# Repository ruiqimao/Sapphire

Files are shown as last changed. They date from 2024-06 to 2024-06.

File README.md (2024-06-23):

# Sapphire

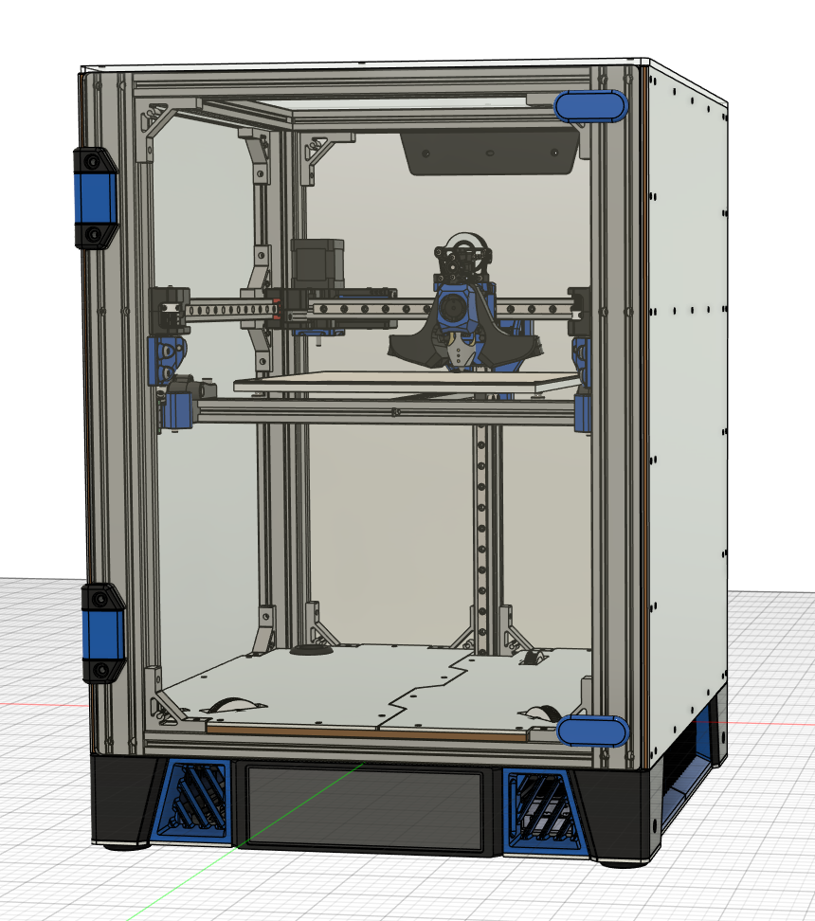
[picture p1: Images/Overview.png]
Overview


Sapphire is a 250x250x230 CoreXY printer primarily featuring components from other projects:

* [Monolith gantry](https://github.com/CloakedWayne/Monolith_Gantry_V2-VT)
* [Archetype toolhead](https://github.com/Armchair-Heavy-Industries/Archetype)
* [Annex Engineering K3 Z system](https://github.com/Annex-Engineering/Gasherbrum-K3)
* [Voron Trident bed](https://github.com/VoronDesign/Voron-Trident)
* 4040/2020 frame members
* Aluminum structural panels
* Slide out electronics bay
* Dual PSUs for mixed 24V and 48V components
* Dual SSRs for optional chamber heating
* [7.9" Waveshare DSI display](https://www.waveshare.com/7.9inch-dsi-lcd.htm)

## CAD

* CAD drawings for original design elements are included in [CAD/Base/Sapphire.zip](CAD/Base/Sapphire.zip).
* Monolith and Archetype components can be found in their respective repositories.
* Modified version of K3Z can be found in [CAD/Z Components/Z Components.zip](<CAD/Z Components/Z Components.zip>), along with a copy of the Annex Engineering license agreement.

## STLs

No STLs are provided. Everything is available from CAD or external repositories.

## Misumi codes

The extrusions and brackets used for the frame, bed, and electronics are:

### Frame
```
4x HFS5-4040-550-SC-LCP-RCP-AV360
9x HFS5-2040-370-TPW-SC
1x HFS5-2040-370-TPW-SC-AH185
1x HFS5-2040-330-TPW-SC
1x HFS5-2020-240-SC
1x HFS5-2020-370-SC
```

### Bed
```
1x HFS5-2020-340-TPW-SC-AH170
1x HFS5-2020-255-TPW-SC
```

### Electronics
```
2x HFS5-2020-300
```

### Corner brackets
```
31x HBKUS5
```

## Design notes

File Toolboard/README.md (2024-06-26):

# Sapphire Toolboard

> [!WARNING]
> Archetype is in beta and is subject to change. Use this toolboard knowing that compatibility may break in the future.

<p float="left">
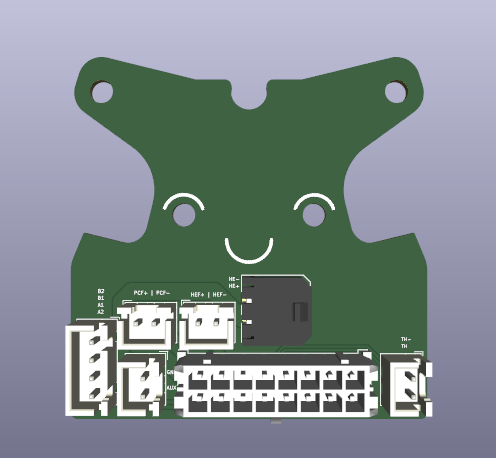
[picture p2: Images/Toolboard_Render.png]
  
  
</p>

These are the files used to produce and mount the toolhead PCB used in Sapphire.

## Production requirements

* 1.6mm thick
* 2 layers
* 1oz minimum (2oz preferred)

## Mounting

The toolboard is clamped between the Sherpa Mini and extruder block, as shown here:

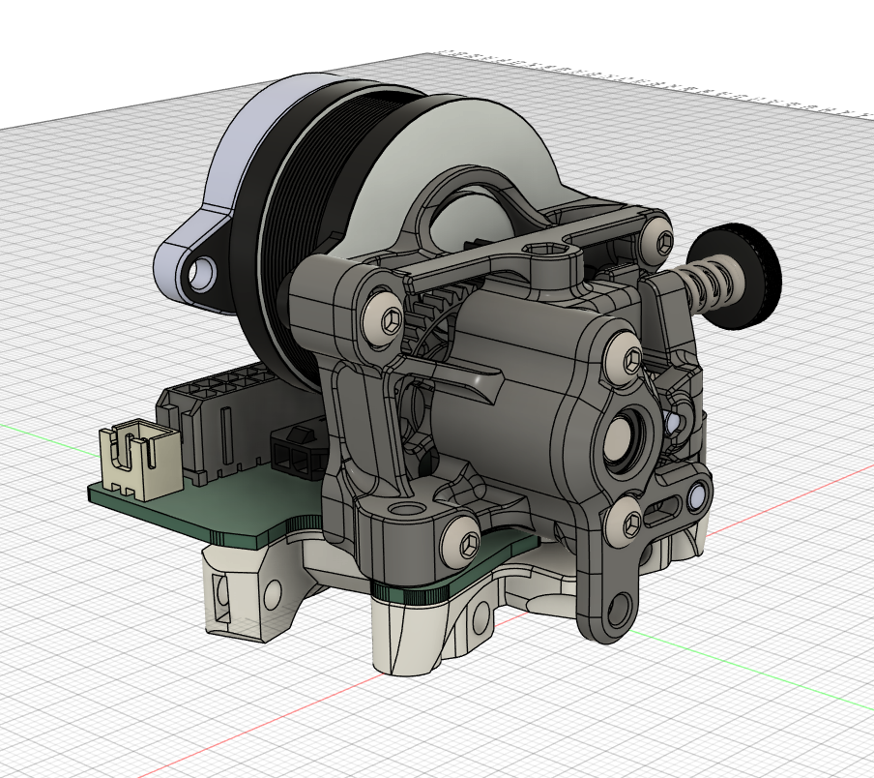
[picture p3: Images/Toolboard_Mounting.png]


## STLs

* K_Face.stl: An altered K-Face for the Sherpa Mini is necessary due to the thickness of the PCB.
* Strain_Relief.stl: Mounted to the back of the stepper motor to provide strain relief.

## Harness and distribution board

Pinout and harness compatible with [Xol PCB](https://github.com/ruiqimao/VoronStuff/tree/main/Xol_PCB).

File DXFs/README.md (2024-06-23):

# DXFs

## Materials

### 3.2mm Aluminum
* Back
* Deck_Left
* Deck_Right
* Electronics
* Side
* Skirt

### 5.6mm Polycarbonate
* Front Door
* Top

## Notes

* Two copies of Side_x2.dxf and Skirt_x2.dxf are needed.
* Electronics.dxf contains holes meant to be tapped for PSU and SSR mounting:
  * M3: 2.6mm holes
  * M4: 3.41mm holes
* Front_Door.dxf requires the holes mounted to the hinges to be countersunk.

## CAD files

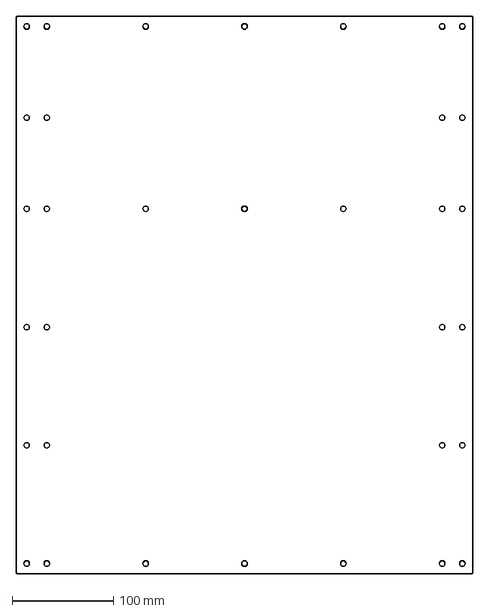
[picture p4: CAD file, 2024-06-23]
DXFs/Side_x2.dxf
450.0 x 550.0 mm

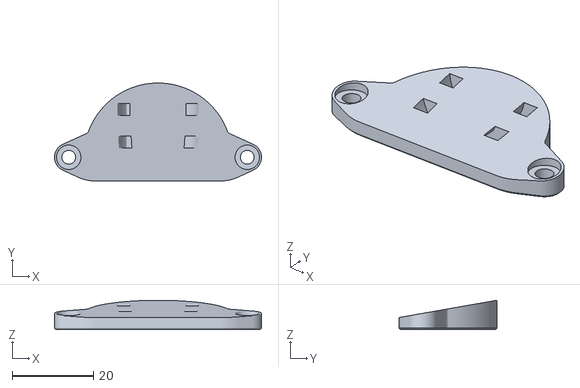
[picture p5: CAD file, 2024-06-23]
Toolboard/STLs/Strain_Relief.stl
50.9 x 24.1 x 7.25

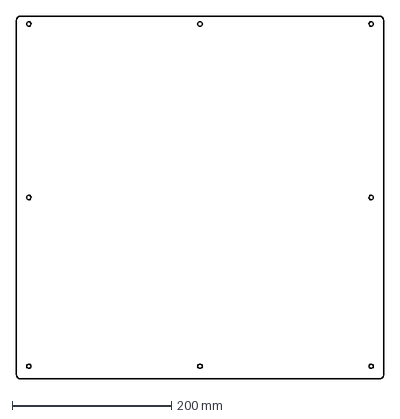
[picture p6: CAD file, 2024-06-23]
DXFs/Top.dxf
462.0 x 456.0 mm

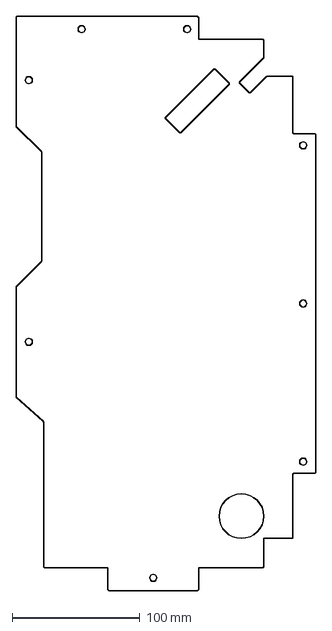
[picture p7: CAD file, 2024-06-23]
DXFs/Deck_Left.dxf
235.0 x 450.0 mm

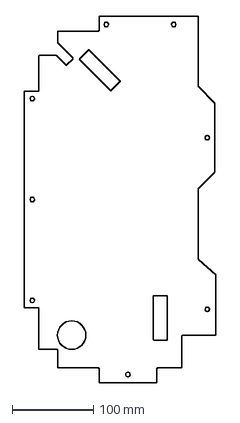
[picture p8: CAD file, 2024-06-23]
DXFs/Deck_Right.dxf
235.5 x 450.0 mm

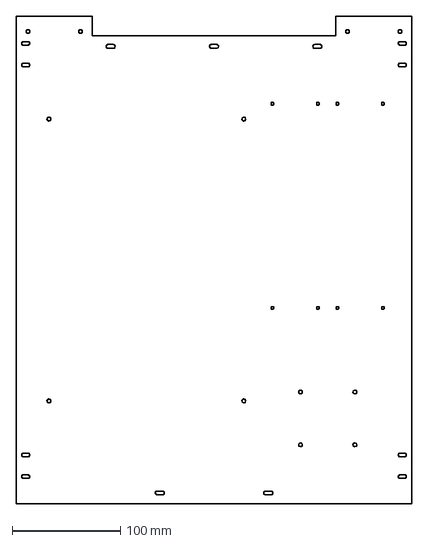
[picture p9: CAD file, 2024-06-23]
DXFs/Electronics.dxf
365.0 x 450.0 mm

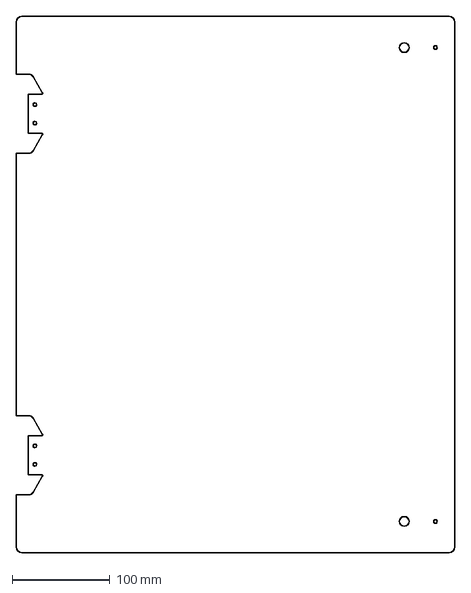
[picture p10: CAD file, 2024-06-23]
DXFs/Front_Door.dxf
450.0 x 550.0 mm

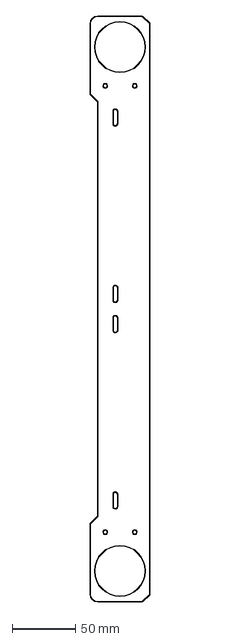
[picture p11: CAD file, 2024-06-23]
DXFs/Skirt_x2.dxf
47.4 x 462.6 mm

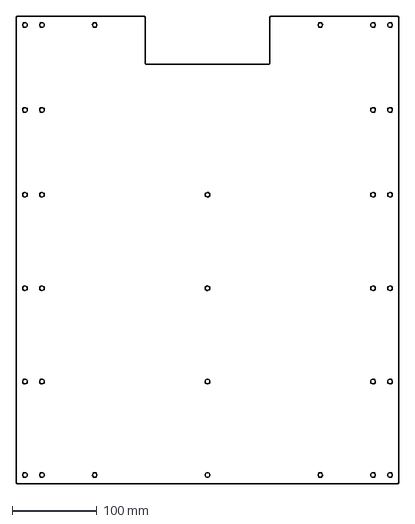
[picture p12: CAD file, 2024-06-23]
DXFs/Back.dxf
450.0 x 550.0 mm

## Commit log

2024-06-23 Rename Front Door.dxf to Front_Door.dxf
    [Front_Door.dxf]
2024-06-23 Remove bed from Z Components
2024-06-23 Add toolboard gerbers
2024-06-23 Fix silkscreen
2024-06-23 Add STLs and mounting image for toolboard
    [K_Face.stl, Strain_Relief.stl]
2024-06-23 Remove extra copy of k face
    [K_Face.stl]
2024-06-23 Remove extra copy of strain relief
    [Strain_Relief.stl]
2024-06-23 Reorient strain relief
    [Strain_Relief.stl]
